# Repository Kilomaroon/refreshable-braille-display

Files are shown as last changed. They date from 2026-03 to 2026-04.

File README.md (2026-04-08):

# refreshable-braille-display
The braille reader in the 3D printed casing
The PCB for the braille reader

## Background
In 2016, [Statistics Canada](https://www150.statcan.gc.ca/n1/en/catalogue/89-654-X) found that nearly 3% of Canadians, aged 15 years and older, identify as having a vision impairment which limits their daily activities. Within this group, 5.8% are legally blind. The same survey found that the same demographic had overall lower levels of educational attainment compared with those who did not have any disability. More recently, the [2019 Canadian Income Survey](https://www150.statcan.gc.ca/n1/daily-quotidien/230627/dq230627b-eng.htm) reported that Canadians aged 16 and older with disabilities earned an average of $11,500 less per year than those without disabilities ($43,400 versus $55,200). These statistics highlight significant barriers to literacy and employment for individuals with vision impairment.

Everyone deserves the opportunity to read and access information, regardless of visual ability or financial circumstance, however, commercial braille readers remain prohibitively expensive for many individuals. Braille readers allow blind users to read and write text directly through touch, promoting true literacy and independence that audio devices alone cannot provide. Currently available [commercial braille readers](https://specialneedscomputers.ca/products/orbit-reader-20-plus) typically range from $2800 to [over $4000 CAD](https://store.humanware.com/hca/mantis-q40.html). 

**The purpose of this project is to develop a Refreshable Braille display that is more affordable. All files are available to anyone and we encourage people to modify and improve upon it.**

## Functionality
The user creates a text file called `text.txt` on a micro SD card and plugs it into the external memory card reader. The user then uses the forward and backward input buttons can read the resulting output on the braille cells. The device is battery operated and it is easy to change the number of cells via editing the code in `firepins.c`.

## Design
The program consists of a basic implementation for reading a FAT32 cluster from an SD card connected to the system. It then stores this cluster in a buffer and translate it to a binary encoding for the braille pins. The program currentl supports ascii characters a-z,A-Z, 0-9, and a handful of special characters. Future improvement for this project would include a more memory-effective encoding for the braille cells and implementation of [elm-chan's FATFS](https://elm-chan.org/fsw/ff/).

Example debug output

The PCB, braille cell models, and casing files can also be found here, and can be modified if desired. The braille cell design is based on [this project](https://hackaday.io/project/191181-electromechanical-refreshable-braille-module). Several modifications had to be made to the original design based on cost, feasibility, and project availability.

Example braille cell

## Results
Multiple braille cells integrable into PCB for line display of up to 16 characters. Individual braille cell is able to display characters with ~90% pin firing accuracy

From our testing the batteries have a service life of ~3 hours before the voltage drops below usable levels. Since the braille cells require 3.5V (after 1.5V buck converter voltage drop) to reliably operate, they are the limiting factor on service life.
Picture of buck converter at 3.3 output volts

Each braille cell can be manufactured for ~$9.50, accounting for damaged parts during fabrication. Overall the device can be made for $380.

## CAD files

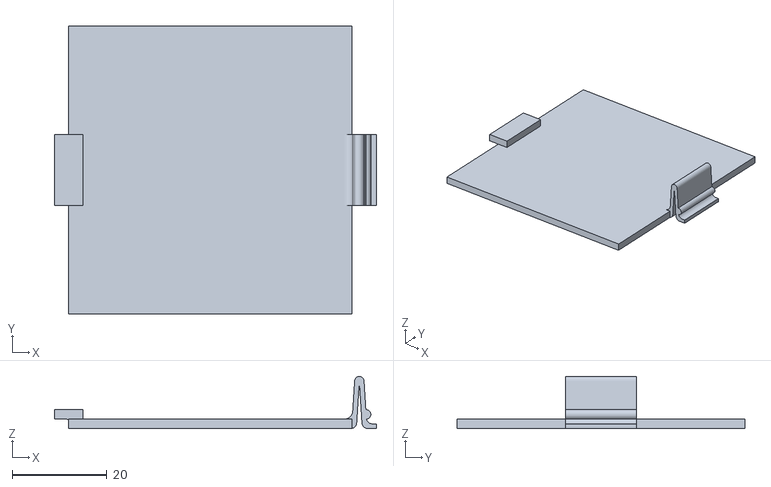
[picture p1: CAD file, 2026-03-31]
casing/Battery Cover V1.1.stl
67.9 x 60.8 x 11.0

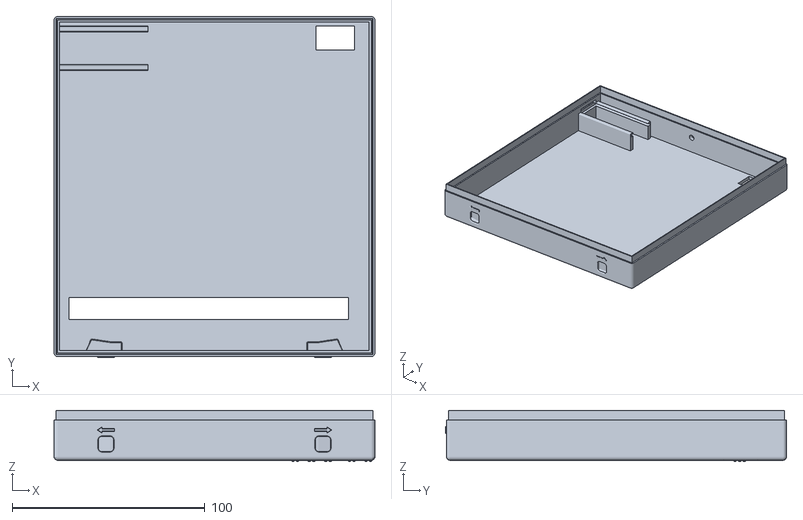
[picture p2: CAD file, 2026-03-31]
casing/Casing Top V2.5.stl
166.6 x 177.1 x 26.7

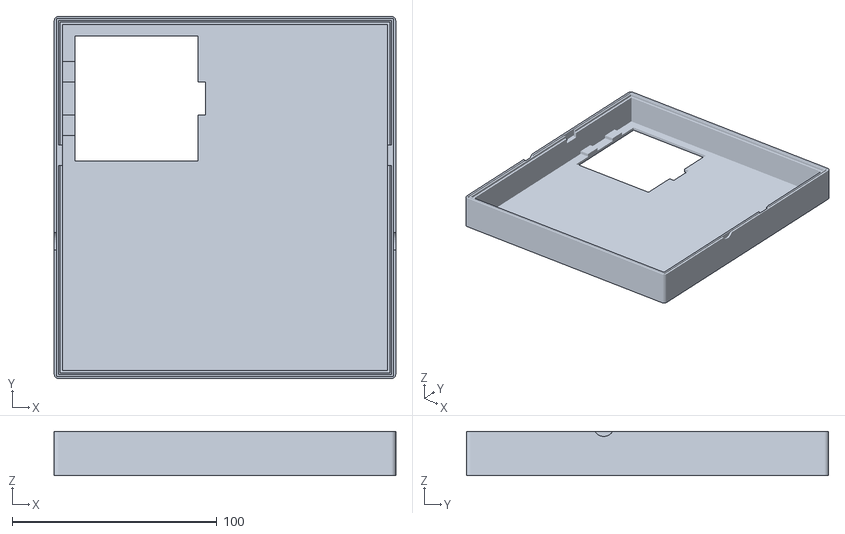
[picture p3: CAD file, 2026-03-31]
casing/Casing Bottom V2.4.stl
166.6 x 176.6 x 21.6

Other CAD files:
Braille 20.1.f3z

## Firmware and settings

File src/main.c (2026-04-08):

#include <avr/io.h>
#include <stdio.h>
#include <string.h>
#include <avr/pgmspace.h>
#include <stdint.h>
#define F_CPU 8000000UL
#include <util/delay.h>
#include "uart.h"
#include "spi.h"
#include "sdcard.h"
#include "sdprint.h"
#include "firepins.h"


#define BAUD_RATE 9600
#define P1_OFFSET 446

#define ATTR_READ_ONLY 0x01
#define ATTR_HIDDEN 0x02
#define ATTR_SYSTEM 0x04
#define ATTR_VOLUME_ID 0x08
#define ATTR_DIRECTORY 0x10
#define ATTR_ARCHIVE 0x20
#define ATTR_LONG_NAME 0x0F
#define LAST_LONG_ENTRY 0x01

int main(void)
{
    
    _Bool FileFound = 0;
    
    // array to hold responses
    uint8_t res[5], buf[512], token;
    uint32_t addr = 0;
    
    // Partition Data
    uint8_t Partition_Type_Code;
    uint32_t Partition_LBA_Begin, Number_of_Sectors;
    
    // LBA Data
    uint8_t BPB_SecPerClus, BPB_NumFATs;
    uint16_t BPB_BytsPerSec, BPB_RsvdSecCnt;
    uint32_t BPB_FATSz32, BPB_RootClus, BPB_TotSec32;
    
    
    
    
    // initialize UART
    UART_init();

    // initialize SPI
    SPI_init(SPI_MASTER | SPI_FOSC_128 | SPI_MODE_0);

    // initialize sd card
    if(SD_init() != SD_SUCCESS)
    {
        UART_pputs("Error initializing SD CARD\r\n");
    }
    else
    {
        UART_pputs("SD Card initialized\r\n");

        // read sector 0
        UART_pputs("\r\nReading Address: 0x");
        UART_puthex8((uint8_t)(addr >> 24));
        UART_puthex8((uint8_t)(addr >> 16));
        UART_puthex8((uint8_t)(addr >> 8));
        UART_puthex8((uint8_t)addr);
        res[0] = SD_readSingleBlock(addr, buf, &token);
        UART_pputs("\r\nResponse:\r\n");
        SD_printR1(res[0]);

        if(!(token & 0xF0))
        {
            UART_pputs("Error token:\r\n");
            SD_printDataErrToken(token);
        }
        
        Partition_Type_Code = buf[P1_OFFSET+4];
        Partition_LBA_Begin = ((uint32_t)buf[P1_OFFSET+11] << 24) |((uint32_t)buf[P1_OFFSET+10] << 16) |((uint32_t)buf[P1_OFFSET+9] << 8) | (uint32_t)buf[P1_OFFSET+8];
        Number_of_Sectors = ((uint32_t)buf[P1_OFFSET+15] << 24) |((uint32_t)buf[P1_OFFSET+14] << 16) |((uint32_t)buf[P1_OFFSET+13] << 8) | (uint32_t)buf[P1_OFFSET+12];
        
        UART_pputs("\r\nPartition Type Code: 0x");
        UART_puthex8(Partition_Type_Code);
        
        UART_pputs("\r\nNumber of Sectors: 0x");
        UART_puthex32(Number_of_Sectors);
        
        addr = Partition_LBA_Begin;
        
        res[0] = SD_readSingleBlock(addr, buf, &token);
        
        // read sector LBA
        UART_pputs("\r\nReading Address: 0x");
        UART_puthex8((uint8_t)(addr >> 24));
        UART_puthex8((uint8_t)(addr >> 16));
        UART_puthex8((uint8_t)(addr >> 8));
        UART_puthex8((uint8_t)addr);
        res[0] = SD_readSingleBlock(addr, buf, &token);
        UART_pputs("\r\nResponse:\r\n");
        SD_printR1(res[0]);
        
        if(!(token & 0xF0))
        {
            UART_pputs("Error token:\r\n");
            SD_printDataErrToken(token);
        }
        
        BPB_BytsPerSec = (buf[12] << 8) | buf[11];
        BPB_SecPerClus = buf[13];
        BPB_FATSz32 = ((uint32_t)buf[39] << 24) |((uint32_t)buf[38] << 16) |((uint32_t)buf[37] << 8) | (uint32_t)buf[36];
        BPB_NumFATs = buf[16];
        BPB_RsvdSecCnt = (buf[15] << 8) | buf[14];
        BPB_RootClus = ((uint32_t)buf[47] << 24) |((uint32_t)buf[46] << 16) |((uint32_t)buf[45] << 8) | (uint32_t)buf[44];
        BPB_TotSec32 = ((uint32_t)buf[35] << 24) |((uint32_t)buf[34] << 16) |((uint32_t)buf[33] << 8) | (uint32_t)buf[32];
        
        
        UART_pputs("\r\nBytes Per Sector: 0x");
        UART_puthex16(BPB_BytsPerSec);
        
        UART_pputs("\r\nSectors Per Cluster: 0x");
        UART_puthex8(BPB_SecPerClus);
        
        UART_pputs("\r\nNumber of Reserved Sectors: 0x");
        UART_puthex16(BPB_RsvdSecCnt);
        
        UART_pputs("\r\nNumber of FATs: 0x");
        UART_puthex8(BPB_NumFATs);
        
        UART_pputs("\r\nSectors Per FAT: 0x");
        UART_puthex32(BPB_FATSz32);
        
        UART_pputs("\r\nRoot Directory First Clusters: 0x");
        UART_puthex32(BPB_RootClus);
        
        UART_pputs("\r\nTotal Sector Count: 0x");
        UART_puthex32(BPB_TotSec32);
        
        
        // SD working variables
        uint32_t FAT32ClusEntryVal, FirstDataSector, FirstSectorofCluster, N, FATOffset,ThisFATSecNum,ThisFATEntOffset ;
        
        
        N = BPB_RootClus;
        
        FirstDataSector = BPB_RsvdSecCnt + (BPB_NumFATs * BPB_FATSz32);
        FirstSectorofCluster = ((N - 2) * BPB_SecPerClus) + FirstDataSector;
        
        FATOffset = N * 4;
        ThisFATSecNum = BPB_RsvdSecCnt + (FATOffset/BPB_BytsPerSec);
        ThisFATEntOffset = FATOffset % BPB_BytsPerSec;
            
        UART_pputs("\r\nRoot Directory...");
        addr = FirstDataSector + Partition_LBA_Begin;
        res[0] = SD_readSingleBlock(addr, buf, &token);
        if((res[0] == 0x00) && (token == SD_START_TOKEN))
            SD_printBufAscii(buf);
            SD_printBuf(buf);
            
        UART_pputs("\r\n");
            
        uint32_t DIR_FileSize;
        uint8_t DIR_Name[11], DIR_Attr, LDIR_Ord;
        uint8_t LDIR_Attr, TargetFile[]="TEXT    TXT"; // Note that the file has to be named text.txt. Change this to change the file we seek
        uint8_t LFN[255], LFN_Buf[255];
        int i = 0;
        
        while (i<SD_BLOCK_LEN){
            LDIR_Attr = buf[11+i];
            LDIR_Ord = buf[i];
            DIR_Attr = buf[11+i];
            
            if ((LDIR_Attr == ATTR_LONG_NAME) && (LDIR_Ord != 0xE5)){
                for (int m = 0; m < 255; m++){ // reset LFN
                    LFN[m] = '\0';
                    LFN_Buf[m] = '\0';
                }
                int k = 0;
                while ((LDIR_Ord >= 0x01) && (LDIR_Ord <= 0x42)){
                    for (int j = 0; j<10;j++){
                        LFN[(k)*26 + j]=buf[i+j+1];
                    }
                    for (int j = 0; j<12;j++){
                        LFN[(k)*26+10+ j]=buf[i+j+14];
                    }
                    for (int j = 0; j<4;j++){
                        LFN[(k)*26+22+j]=buf[i+j+28];
                    }
                    k+=1;
                    i+=32;
                    LDIR_Ord = buf[i];
                }
                
                UART_pputs("\r\nLFN: ");
                

                for (int j = 0; j <= k; j++){
                    for (int m = 0; m<26; m++){
                        LFN_Buf[m+26*j] = LFN[m+26*(k-j)];
                    }
                }
                
                for (int m = 0; m < 255; m++) {
                    LFN[m] = LFN_Buf[m];
                    UART_putc(LFN[m]);
                }
                
            } 
            else if (LDIR_Ord == 0) {
                i=1000;
            }
            else
            {
                if ((DIR_Attr & (ATTR_DIRECTORY | ATTR_VOLUME_ID)) == 0x00){
                    /* Found a file. */
                    for (int j = 0; j<11;j++){
                        DIR_Name[j] = buf[i+j];
                        UART_putc(DIR_Name[j]);
                    }
                    if (strcmp((const char*)DIR_Name, (const char*)TargetFile) ==0){
                        UART_pputs("\r\nFound text file: ");
                        N = ((uint32_t)buf[i+21] << 24) |((uint32_t)buf[i+20] << 16) |((uint32_t)buf[i+27] << 8) | (uint32_t)buf[i+26];
                        DIR_FileSize = ((uint32_t)buf[i+21] << 31) |((uint32_t)buf[i+30] << 16) |((uint32_t)buf[i+29] << 8) | (uint32_t)buf[i+28];
                        UART_pputs("\r\n    Size: 0x");
                        UART_puthex32(DIR_FileSize);
                        FileFound =1;
                    }
                    
                    i+=32;
                }
                else if ((DIR_Attr & (ATTR_DIRECTORY | ATTR_VOLUME_ID)) == ATTR_DIRECTORY){
                    /* Found a directory. */
                    UART_pputs("\r\nFound a directory: ");
                    for (int j = 0; j<11;j++){
                        DIR_Name[j] = buf[i+j];
                        UART_putc(DIR_Name[j]);
                    }
                    i+=32;
                }
                else if ((DIR_Attr & (ATTR_DIRECTORY | ATTR_VOLUME_ID)) == ATTR_VOLUME_ID){
                    /* Found a volume label. */
                    UART_pputs("\r\nFound a volume label: ");
                    for (int j = 0; j<11;j++){
                        DIR_Name[j] = buf[i+j];
                        UART_putc(DIR_Name[j]);
                    }
                    i+=32;
                }
                else{
                    /* Found an invalid directory entry. */
                    UART_pputs("\r\nInvalid");
                    i=1000;
                    i+=32;
                }
            }
            
            
            
        }
      
        if (FileFound){
            FirstDataSector = BPB_RsvdSecCnt + (BPB_NumFATs * BPB_FATSz32);
            FirstSectorofCluster = ((N - 2) * BPB_SecPerClus) + FirstDataSector;

            FATOffset = N * 4;
            ThisFATSecNum = BPB_RsvdSecCnt + (FATOffset/BPB_BytsPerSec);
            ThisFATEntOffset = FATOffset % BPB_BytsPerSec;

            addr = (ThisFATSecNum+BPB_FATSz32) + Partition_LBA_Begin;
            res[0] = SD_readSingleBlock(addr, buf, &token);

            FAT32ClusEntryVal = ((uint32_t)buf[ThisFATEntOffset+3] << 24) |((uint32_t)buf[ThisFATEntOffset+2] << 16) |((uint32_t)buf[ThisFATEntOffset+1] << 8) | (uint32_t)buf[ThisFATEntOffset];
            FAT32ClusEntryVal &= 0x0FFFFFFF;

            UART_pputs("\r\nREADING BEGIN :\r\n");

            for (int m = 0; m <= DIR_FileSize/BPB_BytsPerSec; m++){
                addr = FirstSectorofCluster + Partition_LBA_Begin + m;
                res[0] = SD_readSingleBlock(addr, buf, &token);
                
                SD_printBufAscii(buf);

//                UART_pputs("\r\n20L Test Buf :\r\n");
                fire(buf, DIR_FileSize);
                
                while(1){}
            }
        }
        
        
    }

    while(1) ;
}

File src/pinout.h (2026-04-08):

/* 
 * Author: kilomaroon
 */


#ifndef PINOUT_H
#define    PINOUT_H

/* BUTTONS */
#define DDRbtn DDRC
#define PORTbtn PORTC
#define PINbtn PINC

#define FWDBTN PC0
#define BCKBTN PC1

/* SET/RESET ENABLE */
// array 1
#define DDRr_1 DDRD
#define DDRs_1 DDRC
#define PORTr_1 PORTD
#define PORTs_1 PORTC

#define SET_1 PC5
#define RESET_1 PD0

#define S_MODE_1 PORTr_1 |= (1<<RESET_1); \
PORTs_1 &= ~(1<<SET_1);

#define R_MODE_1 PORTs_1 |= (1<<SET_1); \
PORTr_1 &= ~(1<<RESET_1);

#define N_MODE_1 PORTr_1 &= ~(1<<RESET_1);\
PORTs_1 &= ~(1<<SET_1);

// array 2
#define DDRr_2 DDRB
#define DDRs_2 DDRD
#define PORTr_2 PORTB
#define PORTs_2 PORTD

#define SET_2 PD4
#define RESET_2 PB1

#define S_MODE_2 PORTr_2 |= (1<<RESET_2); \
PORTs_2 &= ~(1<<SET_2);

#define R_MODE_2 PORTs_2 |= (1<<SET_2); \
PORTr_2 &= ~(1<<RESET_2);

#define N_MODE_2 PORTr_2 &= ~(1<<RESET_2);\
PORTs_2 &= ~(1<<SET_2);

/*----------------------------------------------*/
/* DECODER SELECTS - ARRAY 2                    */
/*----------------------------------------------*/

/* PIN SELECT */

// ARRAY 1

// pin select direction register
#define DDR_PS1 DDRC
// pin select output register
#define PORT_PS1 PORTC
// P2_0:2 - decoder pin selects
#define P1_0 PC4
#define P1_1 PC3
#define P1_2 PC2

// ARRAY 2

// pin select direction register
#define DDR_PS2_1 DDRB
#define DDR_PS2_2 DDRD
// pin select output register
#define PORT_PS2_1 PORTB
#define PORT_PS2_2 PORTD
// P2_0:2 - decoder pin selects
#define P2_0 PD5
#define P2_1 PB7
#define P2_2 PB6

/* CELL SELECT */

// ARRAY 1
// cell select direction register
#define DDR_CS1 DDRD
// cell select output register
#define PORT_1 PORTD
// C0:2 - decoder pin selects
#define C1_2 PD1
#define C1_1 PD2
#define C1_0 PD3

// ARRAY 2
// cell select direction register
#define DDR_CS2_1 DDRD
#define DDR_CS2_2 DDRB
// cell select output register
#define PORT_2_1 PORTD
#define PORT_2_2 PORTB
// C0:2 - decoder pin selects
#define C2_2 PD6
#define C2_1 PD7
#define C2_0 PB0

/* SETS */

/* Format: P refers to pin select, A:F refers to braille pin*/
/* A  D */
/* B  E */
/* C  F */

#define CELL1_MASK (1<<P1_0)|(1<<P1_1)|(1<<P1_2)

#define RESETPINS_1 PORT_PS1 |= (1<<P1_0)|(1<<P1_1)|(1<<P1_2);

#define A_1 PORT_PS1 = (PORT_PS1|CELL1_MASK)& ~((1<<P1_2)|(1<<P1_1)|(1<<P1_0)) ;

#define B_1 PORT_PS1 = (PORT_PS1|CELL1_MASK)& ~((1<<P1_2)|(1<<P1_1)) ; 

#define C_1 PORT_PS1 = (PORT_PS1|CELL1_MASK)& ~((1<<P1_2)|(1<<P1_0)) ;

#define D_1 PORT_PS1 = (PORT_PS1|CELL1_MASK)& ~((1<<P1_2)) ;

#define E_1 PORT_PS1 = (PORT_PS1|CELL1_MASK)& ~((1<<P1_1)|(1<<P1_0)) ;

#define F_1 PORT_PS1 = (PORT_PS1|CELL1_MASK)& ~((1<<P1_1)) ;

#define CS1_1  PORT_1 |= ((1<<C1_1)|(1<<C1_2)|(1<<C1_0)); 

#define CS1_2  PORT_1 &= ~((1<<C1_0)); \
PORT_1 |= ((1<<C1_1)|(1<<C1_2)); 

#define CS1_3  PORT_1 &= ~((1<<C1_1)); \
PORT_1 |= ((1<<C1_0)|(1<<C1_2));  

#define CS1_4 PORT_1 &= ~((1<<C1_0)|(1<<C1_1)); \
PORT_1 |= ((1<<C1_2)); 

#define CS1_5 PORT_1 &= ~((1<<C1_2)); \
PORT_1 |= ((1<<C1_0)|(1<<C1_1)); 

#define CS1_6 PORT_1 &= ~((1<<C1_0)|(1<<C1_2)); \
PORT_1 |= ((1<<C1_1)); 

#define CS1_7 PORT_1 &= ~((1<<C1_1)|(1<<C1_2)); \
PORT_1 |= ((1<<C1_0)); 

#define CS1_8 PORT_1 &= ~((1<<C1_1)|(1<<C1_2)|(1<<C1_0)); 

// ARRAY 2

#define CELL2_MASK1 (1<<P2_1)|(1<<P2_2)
#define CELL2_MASK2 (1<<P2_0)

#define RESETPINS_2 PORT_PS2_1 |= ((1<<P2_1)|(1<<P2_2)); \
PORT_PS2_2 |= (1<<P2_0);

#define A_2 PORT_PS2_1 = (PORT_PS2_1|CELL2_MASK1) & ~((1<<P2_2)|(1<<P2_1)); \
PORT_PS2_2 = (PORT_PS2_2|CELL2_MASK2) & ~(1<<P2_0); 

#define B_2 PORT_PS2_2 = (PORT_PS2_2|CELL2_MASK2); \
PORT_PS2_1 = (PORT_PS2_1|CELL2_MASK1) & ~((1<<P2_1)|(1<<P2_2));

#define C_2 PORT_PS2_2 = (PORT_PS2_2|CELL2_MASK2)  & ~(1<<P2_0); \
PORT_PS2_1 = (PORT_PS2_1|CELL2_MASK1)& ~((1<<P2_2));

#define D_2 PORT_PS2_1 = (PORT_PS2_1|CELL2_MASK1) & ~(1<<P2_2); \
PORT_PS2_2 = (PORT_PS2_2|CELL2_MASK2); 

#define E_2 PORT_PS2_1 = (PORT_PS2_1|CELL2_MASK1) & ~((1<<P2_1)); \
PORT_PS2_2 = (PORT_PS2_2|CELL2_MASK2) & ~(1<<P2_0);

#define F_2 PORT_PS2_1 = (PORT_PS2_1|CELL2_MASK1) & ~(1<<P2_1); \
PORT_PS2_2 = (PORT_PS2_2|CELL2_MASK2);

#define CS2_1 PORT_2_1 |= ((1<<C2_1)|(1<<C2_2)); \
        PORT_2_2 |= ((1<<C2_0));

#define CS2_2 PORT_2_1 |= ((1<<C2_1)|(1<<C2_2)); \
        PORT_2_2 &= ~((1<<C2_0));

#define CS2_3  PORT_2_1 &= ~(1<<C2_1); \
        PORT_2_1 |= (1<<C2_2); \
        PORT_2_2 |= ((1<<C2_0));

#define CS2_4 PORT_2_1 &= ~(1<<C2_1); \
        PORT_2_1 |= (1<<C2_2); \
        PORT_2_2 &= ~((1<<C2_0));

#define CS2_5 PORT_2_1 &= ~(1<<C2_2); \
        PORT_2_1 |= (1<<C2_1); \
        PORT_2_2 |= ((1<<C2_0));

#define CS2_6 PORT_2_1 &= ~(1<<C2_2); \
        PORT_2_1 |= (1<<C2_1); \
        PORT_2_2 &= ~((1<<C2_0));

#define CS2_7 PORT_2_1 &= ~(1<<C2_1); \
        PORT_2_1 &= ~(1<<C2_2); \
        PORT_2_2 |= ((1<<C2_0));

#define CS2_8 PORT_2_1 &= ~(1<<C2_1); \
        PORT_2_1 &= ~(1<<C2_2); \
        PORT_2_2 &= ~((1<<C2_0));


#ifdef    __cplusplus
extern "C" {
#endif

#ifdef    __cplusplus
}
#endif
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

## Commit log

2026-02-04 Basic Single Cell Reset/Set Logic
    Cells will only set an unset pin and reset a set pin. Header file for pinout definitions.
    [main.c, pinout.h]
2026-02-05 Casing CAD Files and Altium files
    [Casing Bottom.f3d, Casing Top.f3d]
2026-03-31 Add files via upload
    Most recent casing files
    [Battery Cover V1.1.stl, Casing Bottom V2.4.stl, Casing Top V2.5.stl]
2026-04-02 organizing files
    [Battery Cover V1.1.stl, Casing Bottom V2.4.stl, Casing Top V2.5.stl]
2026-04-11 Braille Cell Files
    [Braille 20.1.f3z]
